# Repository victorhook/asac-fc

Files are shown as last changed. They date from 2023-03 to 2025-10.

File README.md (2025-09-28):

# ASAC FC

**A** **S**imple **A**nd **C**ool **F**light **C**ontroller (**ASAC FC**) is a completely open-source flight controller that can run on multiple microcontrollers such as:
- rp2040
- rp2350

## Project goals
- [ ] Build a drone with rp2040 devboard + external IMU
- [ ] Build a drone with rp2350 devboard + external IMU
- [ ] Add Stabilize flight mode
- [ ] Add Althold flight mode (requires barometer)
- [ ] Add support for SD card logging
- [ ] UI To configure board
- [X] Separate HAL to build for different platforms (rp2040, sitl etc)

What should be configurable, and what should be built-in to firmware?
### Built-in
Must still be able to boot OK without any of these

### Configurable
- Barometer
- IMU
- RC receiver
- Motor order
- FC orientation

---

TODO: THIS GIF [ASAC Takeoff](docs/asac_takeoff.gif)

## Why rp2040?
It's an incredibly cheap microcontroller that is quite powerful (up to 133 MHz), contains two cores, programmable I/O pins (PIO), seems to ignore the global silicon shortage and has an extensive C/C++ SDK.

## Iteration 2

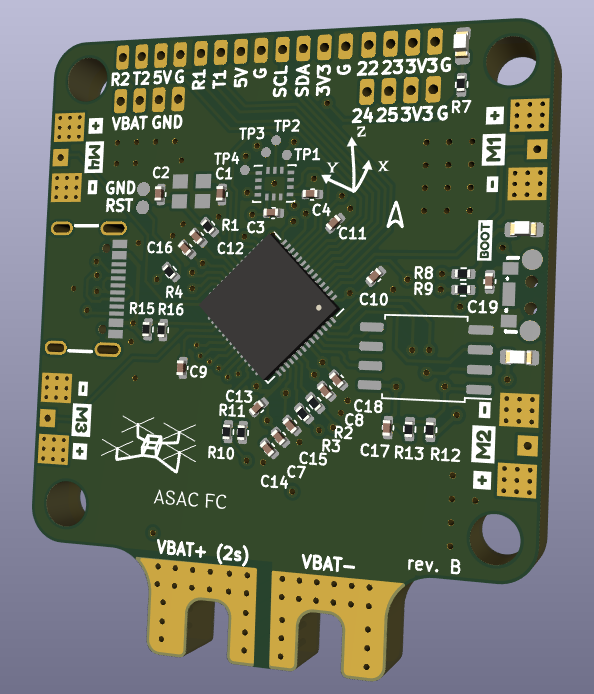
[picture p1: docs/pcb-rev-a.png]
ASAC rev B PCB Kicad

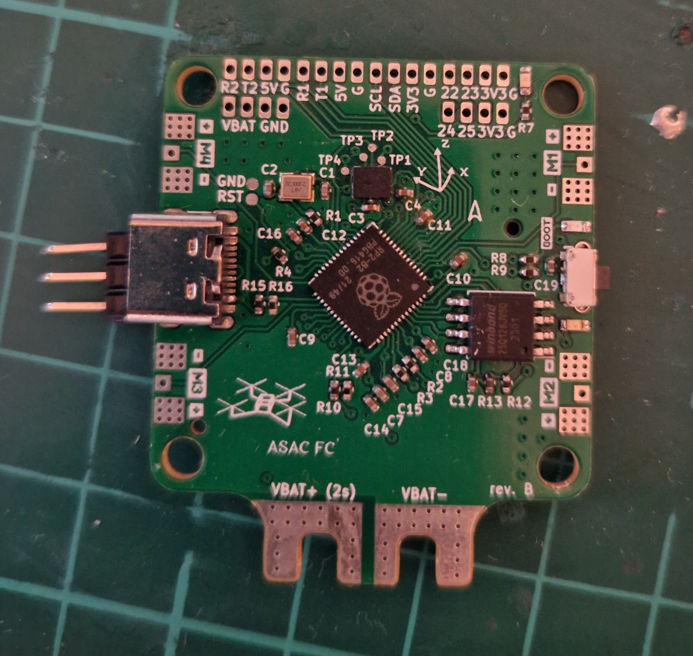
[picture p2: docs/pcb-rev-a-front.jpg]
ASAC rev B PCB front

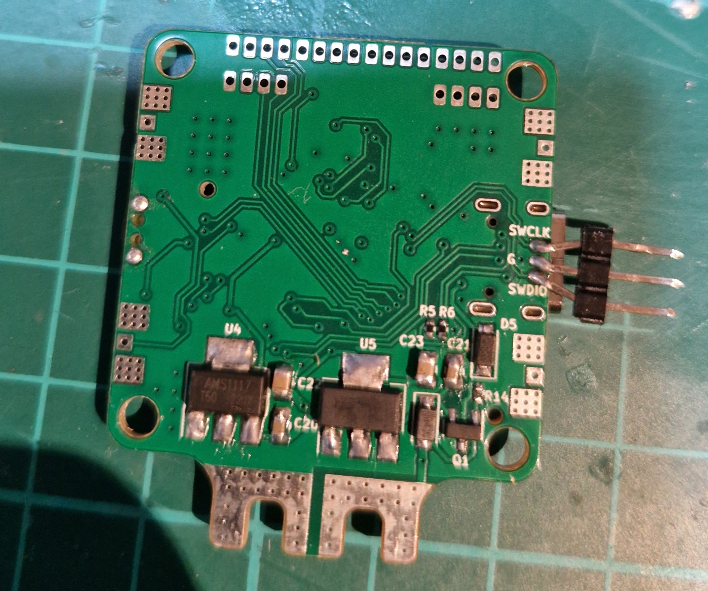
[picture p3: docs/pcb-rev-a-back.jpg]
ASAC rev B PCB back


For the second iteration of the flight controller I designed a PCB in FreeCad, ordered the pcb and components with SMD assembly for the top layer, and soldered the bottom layer myself. All cad files of this can be found in [kicad/asac-fc-rev-b](kicad/asac-fc-rev-b). Schematic can also be found at [documents/asac-fc-rev-b.pdf](documents/asac-fc-rev-b.pdf).
Some nice features of the flight controller PCB are:

- **rp2040** - Flight controller (where asac runs)
- **BMI270** - IMU, using SPI, which allows faster readings than the MPU-6050 which was used for iteration 1.
- **USB-C** - More modern, right? :)
- **Individual ESC solder pads** - Connection for individual ESCs. While most flight stacks today use an 4-in-1 ESC, I decided to keep it simple and use individual ESCs for now.
- **Battery solder pads**

## Iteration 1

The first iteration of *asac fc* was done with development boards, before designing a custom PCB. This is to make a proof of concept, and serves as a sanity check to show that it's possible :). The main components are:
- **Raspberry pi pico** - Flight controller (where asac runs)
- **MPU6050** - IMU
- **FS-a8s** - Radio receiver (Flysky, outputs IBUS)
- **xsd7a ESC** - ESCs (Single motor ESCs, so 4 in total)
- **Frame** - Custom designed, 3D-printed in PLA.

I created a simple power distribution board (brown part, at the bottom of the drone in the picture below), where the battery is connected to. Each ESC as well as the pico and the receiver gets its power from this board. The ESCs are then connected to GPIOs on the pico.

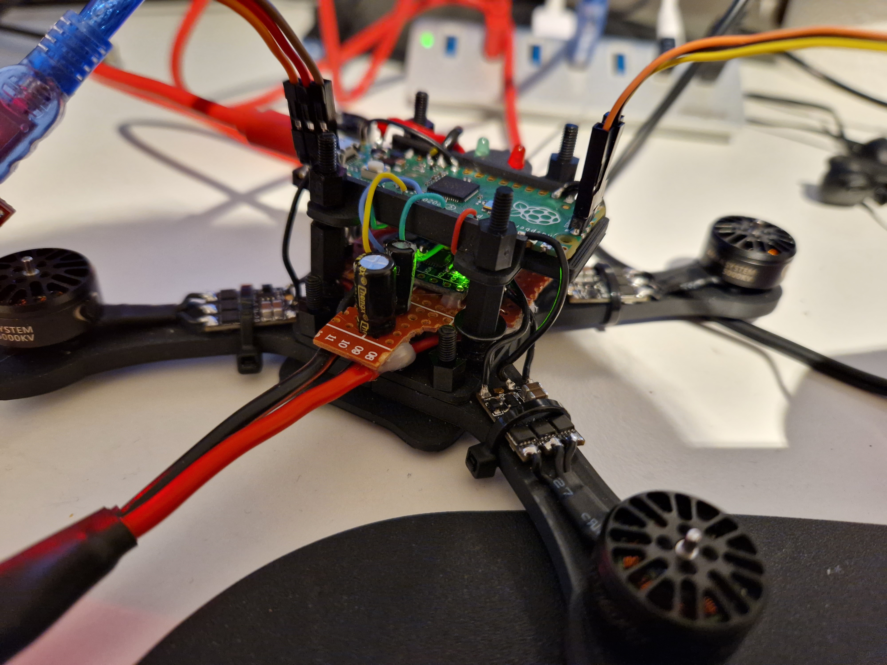
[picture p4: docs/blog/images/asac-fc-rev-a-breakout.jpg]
ASAC FC development


After some manual (headless) flights, I decided to add an analog camera together with a VTX I had laying around. This way, we can fly some FPV with the pico!

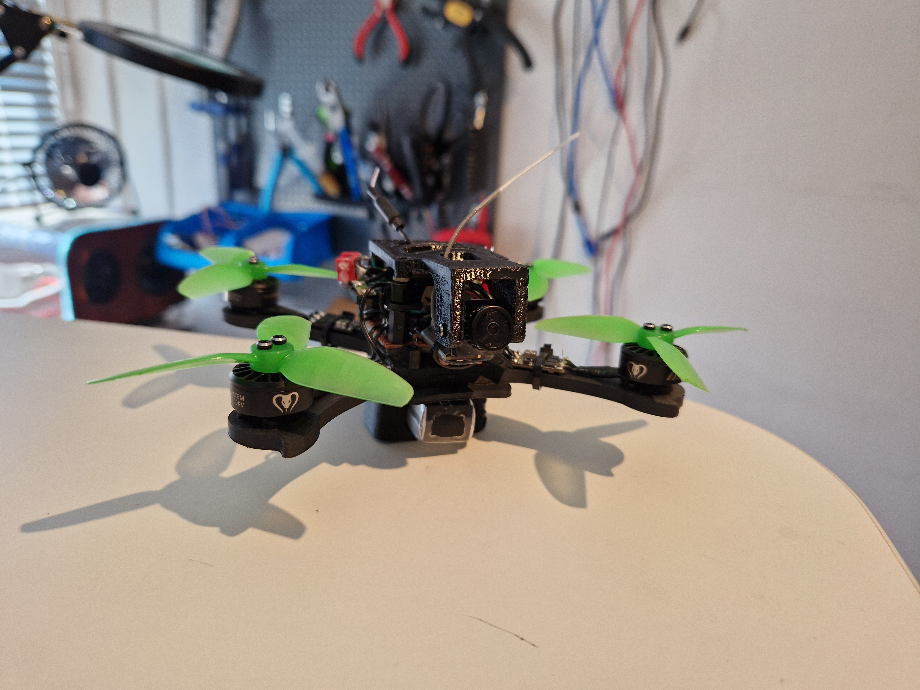
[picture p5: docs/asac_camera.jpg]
ASAC FC


## Features

### Sensors
- [X] IMU
- [ ] GPS
- [ ] Barometer (altitude estimation)
- [ ] Lidar or other distance sensor

### Receiver protocols
- [X] IBUS
- [ ] SBUS
- [ ] Frsky
- [ ] CSRF

### Telemetry
- [ ] Any

### Flight modes
- [X] Acro (attitude rate, aka free-style)
- [ ] Any other stabilizing mode

### ESC Protocols

- [X] PWM (50 hz)
- [X] Oneshot125, utilizing rp2040s PIO block
- [X] Oneshot42, utilizing rp2040s PIO block
- [ ] Multishot
- [ ] Dshot150
- [ ] Dshot300
- [ ] Dshot600
- [ ] Dshot1200
- [ ] ProShot

## From receiver input to motor outputs

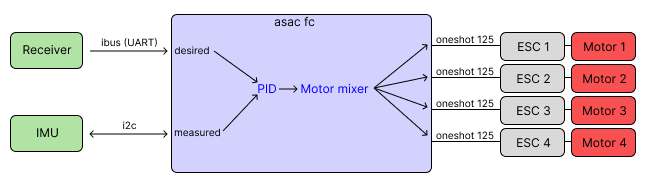
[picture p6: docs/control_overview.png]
Control overview


In order to set the correct speeds for each motor, several steps must be taken. The steps described below is how it's done for *asac fc*. Note that this is for acro mode only (freestyle, using only gyro rates from IMU).

1. Read gyro rates from IMU
2. Remove bias from gyro reading
3. Filter gyro reading
4. Read receiver input
5. Convert receiver stick inputs to desired gyro rates. This is a mapping from eg. 1000-2000 -> -500 to 500 deg/s.
6. Give the *desired* rates together with the *measured* rates to PID controller that uses PID parameters to calculate adjustment values.
7. Give output from PID controller to motor mixer to get commands for each motor.
8. Send the motor outputs to the ESC(s).

## RTOS
*asac fc* uses a very simple RTOS called [vsrtos](https://github.com/victorhook/vsrtos), that uses a priority based non-preemptive scheduling technique to run tasks. While this rtos is quite immature, it works just fine for this application, since *asac fc* doesn't have that many tasks yet.

## Motor mixing

The motor mixer is responsible for deciding which motor should spin and how much. *asac fc* uses the default motor numbers like in the image below, which is the same as the default for betaflight.

Motors

The default motor mix is:

| Motor | Throttle | Roll | Pitch | Yaw |
| --- | --- | --- | --- | --- |
| 1 | 1 | -1 | 1  | -1 |
| 2 | 1 | -1 | -1 | 1  |
| 3 | 1 | 1  | 1  | 1 |
| 4 | 1 | 1  | -1 | -1  |

## Flashing

You can flash the pico through in three different ways:
1. Through USB, when it's connected as a USB device (press down button while powering the pico)
2. Through serial USB by utilizing the picotool:
   `picotool load -f target.uf2 && picotool reboot -f`
    This works if uart 0 is mapped to USB:
    ```
    pico_enable_stdio_uart(asac-fc 0)
    pico_enable_stdio_usb(asac-fc 1)
    ```
    The command above first flashes the target `uf2` file to the pico by forcing it into BOOTSEL mode. We then reset the pico with `picotool reboot -f`. The flag `-f` is crucial here, since it allows us to load and reboot it without being in BOOTSEL mode already. I think it accomplishes this by changing the baud rate of the connection, which forces the pico to BOOTSEL mode, but I am not 100% sure.
3. SWD using debugger/another pico.

## Available build defines

There are several parameters that can be defined on build-time to configure the firmware. All of the defines can also be found in the `CMakeLists.txt` These includes:

| Define | Description |
| --- | --- |
| USE_DEFAULT_SETTINGS | If defined, asac will use default settings and write them to flash. Note that this will erase any previous settings that were stored in flash. This can be useful when using the flight controller for the first time, or updating the data structure of the flash. |
| LINUX | If defined, the firmware is built to be run on a linux machine and *not* for rp2040. This can be useful if you want to run unit tests on certain parts of code, or simulate fc. |
| RP2040 | Used by vsrtos. Do not change |

## Resources
- [Embedded Programming for Quadcopters](https://www.youtube.com/watch?v=CHSYgLfhwUo&ab_channel=Code%26Supply)
- [Motor mixing](https://oscarliang.com/custom-motor-output-mix-quadcopter/)

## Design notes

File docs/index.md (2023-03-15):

# ASAC FC

**A** **S**imple **A**nd **C**ool **F**light **C**ontroller (ASAC FC) is an flight controller based on the rp2040 microcontroller, that is completely open-source.

## From receiver input to motor outputs

In order to set the correct speeds for each motor several steps must be taken. The steps described below is how it's done for ASAC FC. Note that this is for acro mode only.

1. Read gyro rates from IMU
2. Read receiver input
3. Convert receiver stick inputs to desired gyro rates. This is a mapping from eg. 1000-2000 -> -500 to 500 deg/s.
4. Use the *desired* rates together with the *measured* rates in a pid update to update pid parameters.
5. Use the pid parameters to update the motor outputs.
6. Send the motor outputs to the ESC(s).

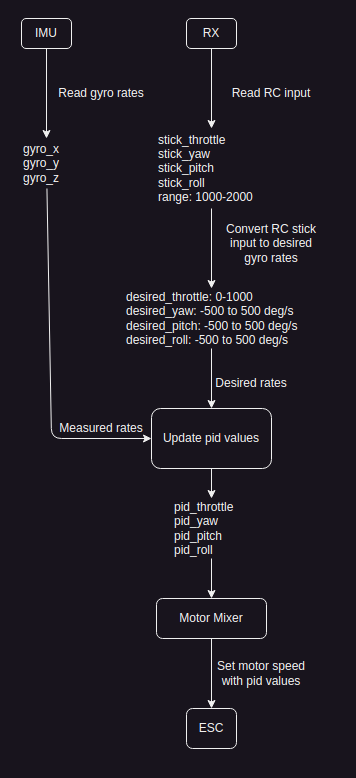
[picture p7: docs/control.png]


## Motor mixing

Motors

| Motor | Throttle | Roll | Pitch | Yaw |
| --- | --- | --- | --- | --- |
| 1 | 1 | -1 | 1  | -1 |
| 2 | 1 | -1 | -1 | 1  |
| 3 | 1 | 1  | 1  | 1 |
| 4 | 1 | 1  | -1 | -1  |

## Resources
- [Embedded Programming for Quadcopters](https://www.youtube.com/watch?v=CHSYgLfhwUo&ab_channel=Code%26Supply)
- [Motor mixing](https://oscarliang.com/custom-motor-output-mix-quadcopter/)

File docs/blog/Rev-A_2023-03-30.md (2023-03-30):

# ASAC FC revision A
For the first revision of the flight controller I designed the PCB in kicad and ordered from JLCPCB. The plan was to solder all components by hand. Unfortunately, I was out of lead-free solder and since I'm not use to working with solder *with* lead, soldering the SMD components such as the IMU (MPU-6050) turned out to be harder than I first anticipated. After several days of struggling, I gave up and switched to using breakout boards and devboard instead.

Raspberry Pi Pico to the rescue, which comes in a rather small package. I also had a breakout board for the IMU. I had to create a power distribution board as well, where the battery will be connected, as well as the ESCs. Even though this does not look as good as a custom PCB, it seems to work just fine.

ASAC-FC rev A. Breakout and devboard

As you can see on the image above, the pico is mounted on top of the power distribution board, which also hosts the IMU and radio receiver. To program the pico I used a [pico debug probe](https://www.raspberrypi.com/products/debug-probe/) and then connected GPIO0 and GPIO1, which are default UART pins, to an FTDI converter connected to my PC.

This way, it was very convenient to program the flash, while constantly being connected to a serial port to its UART, and also having the capability of debugging in VS Code.

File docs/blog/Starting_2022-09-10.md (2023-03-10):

## Introduction
I've built and flown FPV drones for a few years now as a happy and I truly enjoy both building them and flying then. Usually, I end up spending more time building the drones and fixing/repairing them than actually flying then, but for me that is very satisfying. So, during the last two years or so, the prices of electronics for FPV drones has almost doubled. I remember that I bought the first stack of FC + ESC for about 40$, and the very same stack goes for around 70-80$ today. This increase in price together with my own curiosity and maker-mind has made me wanting to build my own FPV electronics for some time, and now it's finally time to take fhe first step!

This is the journey for me building my very first flight controller hardware for an FPV drone. I will design the schematics and PCB in KiCad and order them, together with components, which I will then solder (by hand probably). I'm planning to write my firmware for the FC as well, mainly because I think it's interesting and a fun challenge. My idea is that I will start by making the flight controller, and making the first revision of the drone with my custom flight controller, and all the other parts will be off-the-shelf. Then, perhaps I can create my custom ESC, custom RX, VTX etc, so in the end I will have only custom electronics on my FPV drones! This will probably take a long time however, so for now, let's focus on the flight controller.

## Flight Controller, rev. A
For the first revision, I will have the following main components of the flight controller:
| Component | Description | Motivation |
| --- | --- | --- |
| rp2040 | Main microcontroller | *Very* cheap mcu which is quite new on the market. It has two cores, and I've wanted to use the rp2040 for custom projects for some time now. Since it's supported by the raspberry pi community it has extensive documentation as well as a C SDK. How well this will perform to the famous STM32F4 I do not know yet, so we will have to find out! One thing that does worry me slightly is the lack of UART buses. The rp2040 only has 2 UART buses, *but* it does have programmable IO, which I believe can handle UART communication as well, so it might be possible to extend these 2 buses to more.
| MPU-6050 | Inertial Measurement Unit (IMU) | The famous MPU-6050 must be one of the most popular IMUs for makers in general and on flight controllers. The reason I chose this was simply because I had bought a pack of 10 of these some time ago so I had them laying around. The support for MPU-6050 (in forms of drivers, documentation etc) as well is extensive so there should be no problem to set it up. An important note is that the MPU-6050 is very old and no longer produced, so if this flight controller ever were to become a product, the MPU-6050 must be changed.

Here's some bullet points about some design decisions for revision A:
- There's no OSD chip like MAX7456, or SD card holder simply to keep the scope and complexity down.
- There's solder pads for individual ESCs. Mainly because I had some individual ESCs at home I wanted to use.
- Keep it simple!

Since there's no OSD chip on rev A, I will mainly use this revision to try to get the most basic drone flying working.

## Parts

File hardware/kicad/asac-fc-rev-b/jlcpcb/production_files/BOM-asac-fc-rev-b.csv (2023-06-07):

Comment | Designator | Footprint | LCSC
5.11k | R6 | R_0402_1005Metric
5.11k | R5 | R_0402_1005Metric
D_Schottky | D5 | D_SOD-123
USB_C_Receptacle_USB2.0 | J10 | USB-SMD_GT-USB-7010AN
BMI270 | U1 | BMI270
W25Q128JVSIQ | U3 | SOIC-8_5.23x5.23mm_P1.27mm
30pF | C2 | C_0402_1005Metric
100nF | C13 | C_0402_1005Metric
Conn_01x03 | J4 | Conn_01x03_2big_1small
100nF | C18 | C_0402_1005Metric
Conn_01x03 | J9 | Conn_01x03_2big_1small
330R | R8 | R_0402_1005Metric
330R | R9 | R_0402_1005Metric
100nF | C14 | C_0402_1005Metric
100nF | C12 | C_0402_1005Metric
100nF | C16 | C_0402_1005Metric
Conn_01x02 | J7 | Conn_01x02_small
SW_SPST | SW1 | SW-SMD_TS-1086EV-16
1k | R1 | R_0402_1005Metric
LED | D3 | LED_0603_no_outline
1uF | C7 | C_0402_1005Metric
10k | R4 | R_0402_1005Metric
100nF | C9 | C_0402_1005Metric
Conn_01x03 | J1 | Conn_01x03_2big_1small
27.4R | R3 | R_0402_1005Metric
Conn_01x04 | J15 | Conn_01x04_fpv
1k | R12 | R_0402_1005Metric
10k | R13 | R_0402_1005Metric
CM4012M00020T8188087 | Y1 | Crystal_SMD_2520-4Pin_2.5x2.0mm
RP2040 | U2 | QFN-56-1EP_7x7mm_P0.4mm_EP3.2x3.2mm
1uF | C15 | C_0402_1005Metric
Conn_01x04 | J2 | Conn_01x04_fpv
Conn_01x03 | J14 | PinHeader_1x03_P1.27mm_Vertical_no_silk_smd
10k | R10 | R_0402_1005Metric
Conn_01x04 | J8 | Conn_01x04_fpv
27.4R | R2 | R_0402_1005Metric
100nF | C4 | C_0402_1005Metric
5.6k | R11 | R_0402_1005Metric
100nF | C11 | C_0402_1005Metric
100nF | C8 | C_0402_1005Metric
Conn_01x03 | J6 | Conn_01x03_2big_1small
30pF | C1 | C_0402_1005Metric
LED | D1 | LED_0603_no_outline
Conn_01x04 | J5 | Conn_01x04_fpv
100nF | C17 | C_0402_1005Metric
LED | D2 | LED_0603_no_outline
330R | R7 | R_0402_1005Metric
100nF | C10 | C_0402_1005Metric
Conn_01x04 | J12 | Conn_01x04_fpv
100nF | C3 | C_0402_1005Metric
100nF | C19 | C_0402_1005Metric
AMS1117-5.0 | U4 | SOT-223-3_TabPin2
10uF | C22 | C_0805_2012Metric
D_Schottky | D4 | D_SOD-123
10uF | C20 | C_0805_2012Metric
10uF | C21 | C_0805_2012Metric
AMS1117-3.3 | U5 | SOT-223-3_TabPin2
10uF | C23 | C_0805_2012Metric
10k | R14 | R_0402_1005Metric
Q_PMOS_GSD | Q1 | SOT-23
Conn_01x04 | J3 | Conn_01x04_fpv
TestPoint | TP4 | TP_0.7mm
TestPoint | TP3 | TP_0.7mm
TestPoint | TP2 | TP_0.7mm
TestPoint | TP1 | TP_0.7mm
20k | R16 | R_0402_1005Metric
10k | R15 | R_0402_1005Metric

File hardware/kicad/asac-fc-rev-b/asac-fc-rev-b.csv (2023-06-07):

Source: | /home/victor/coding/projects/asac-fc/kicad/asac-fc-rev-b/asac-fc-rev-b.kicad_sch
Date: | ons 7 jun 2023 19:59:35
Tool: | Eeschema 6.0.11-2627ca5db0~126~ubuntu22.04.1
Generator: | /usr/share/kicad/plugins/bom_csv_grouped_by_value.py
Component Count: | 67
Individual Components:
Item | Qty | Reference(s) | Value | LibPart | Footprint | Datasheet | MANUFACTURER | MAXIMUM_PACKAGE_HEIGHT | PATREV | STANDARD
 |  | C1 | 30pF | Device:C | Capacitor_SMD:C_0402_1005Metric | ~
 |  | C2 | 30pF | Device:C | Capacitor_SMD:C_0402_1005Metric | ~
 |  | C3 | 100nF | Device:C | Capacitor_SMD:C_0402_1005Metric | ~
 |  | C4 | 100nF | Device:C | Capacitor_SMD:C_0402_1005Metric | ~
 |  | C7 | 1uF | Device:C | Capacitor_SMD:C_0402_1005Metric | ~
 |  | C8 | 100nF | Device:C | Capacitor_SMD:C_0402_1005Metric | ~
 |  | C9 | 100nF | Device:C | Capacitor_SMD:C_0402_1005Metric | ~
 |  | C10 | 100nF | Device:C | Capacitor_SMD:C_0402_1005Metric | ~
 |  | C11 | 100nF | Device:C | Capacitor_SMD:C_0402_1005Metric | ~
 |  | C12 | 100nF | Device:C | Capacitor_SMD:C_0402_1005Metric | ~
 |  | C13 | 100nF | Device:C | Capacitor_SMD:C_0402_1005Metric | ~
 |  | C14 | 100nF | Device:C | Capacitor_SMD:C_0402_1005Metric | ~
 |  | C15 | 1uF | Device:C | Capacitor_SMD:C_0402_1005Metric | ~
 |  | C16 | 100nF | Device:C | Capacitor_SMD:C_0402_1005Metric | ~
 |  | C17 | 100nF | Device:C | Capacitor_SMD:C_0402_1005Metric | ~
 |  | C18 | 100nF | Device:C | Capacitor_SMD:C_0402_1005Metric | ~
 |  | C19 | 100nF | Device:C | Capacitor_SMD:C_0402_1005Metric | ~
 |  | C20 | 10uF | Device:C | Capacitor_SMD:C_0805_2012Metric | ~
 |  | C21 | 10uF | Device:C | Capacitor_SMD:C_0805_2012Metric | ~
 |  | C22 | 10uF | Device:C | Capacitor_SMD:C_0805_2012Metric | ~
 |  | C23 | 10uF | Device:C | Capacitor_SMD:C_0805_2012Metric | ~
 |  | D1 | LED | Device:LED | Custom:LED_0603_no_outline | ~
 |  | D2 | LED | Device:LED | Custom:LED_0603_no_outline | ~
 |  | D3 | LED | Device:LED | Custom:LED_0603_no_outline | ~
 |  | D4 | D_Schottky | Device:D_Schottky | Diode_SMD:D_SOD-123 | ~
 |  | D5 | D_Schottky | Device:D_Schottky | Diode_SMD:D_SOD-123 | ~
 |  | J1 | Conn_01x03 | Connector_Generic:Conn_01x03 | Custom:Conn_01x03_2big_1small | ~
 |  | J2 | Conn_01x04 | Connector_Generic:Conn_01x04 | Custom:Conn_01x04_fpv | ~
 |  | J3 | Conn_01x04 | Connector_Generic:Conn_01x04 | Custom:Conn_01x04_fpv | ~
 |  | J4 | Conn_01x03 | Connector_Generic:Conn_01x03 | Custom:Conn_01x03_2big_1small | ~
 |  | J5 | Conn_01x04 | Connector_Generic:Conn_01x04 | Custom:Conn_01x04_fpv | ~
 |  | J6 | Conn_01x03 | Connector_Generic:Conn_01x03 | Custom:Conn_01x03_2big_1small | ~
 |  | J7 | Conn_01x02 | Connector_Generic:Conn_01x02 | Custom:Conn_01x02_small | ~
 |  | J8 | Conn_01x04 | Connector_Generic:Conn_01x04 | Custom:Conn_01x04_fpv | ~
 |  | J9 | Conn_01x03 | Connector_Generic:Conn_01x03 | Custom:Conn_01x03_2big_1small | ~
 |  | J10 | USB_C_Receptacle_USB2.0 | Connector:USB_C_Receptacle_USB2.0 | Custom:USB-SMD_GT-USB-7010AN | https://www.lcsc.com/product-detail/span-style-background-color-ff0-USB-span-Connectors_G-Switch-GT-USB-7010AN_C963370.html
 |  | J12 | Conn_01x04 | Connector_Generic:Conn_01x04 | Custom:Conn_01x04_fpv | ~
 |  | J14 | Conn_01x03 | Connector_Generic:Conn_01x03 | Custom:PinHeader_1x03_P1.27mm_Vertical_no_silk_smd | ~
 |  | J15 | Conn_01x04 | Connector_Generic:Conn_01x04 | Custom:Conn_01x04_fpv | ~
 |  | Q1 | Q_PMOS_GSD | Device:Q_PMOS_GSD | Package_TO_SOT_SMD:SOT-23 | ~
 |  | R1 | 1k | Device:R | Resistor_SMD:R_0402_1005Metric | ~
 |  | R2 | 27.4R | Device:R | Resistor_SMD:R_0402_1005Metric | ~
 |  | R3 | 27.4R | Device:R | Resistor_SMD:R_0402_1005Metric | ~
 |  | R4 | 10k | Device:R | Resistor_SMD:R_0402_1005Metric | ~
 |  | R5 | 5.11k | Device:R | Resistor_SMD:R_0402_1005Metric | ~
 |  | R6 | 5.11k | Device:R | Resistor_SMD:R_0402_1005Metric | ~
 |  | R7 | 330R | Device:R | Resistor_SMD:R_0402_1005Metric | ~
 |  | R8 | 330R | Device:R | Resistor_SMD:R_0402_1005Metric | ~
 |  | R9 | 330R | Device:R | Resistor_SMD:R_0402_1005Metric | ~
 |  | R10 | 10k | Device:R | Resistor_SMD:R_0402_1005Metric | ~
 |  | R11 | 5.6k | Device:R | Resistor_SMD:R_0402_1005Metric | ~
 |  | R12 | 1k | Device:R | Resistor_SMD:R_0402_1005Metric | ~
 |  | R13 | 10k | Device:R | Resistor_SMD:R_0402_1005Metric | ~
 |  | R14 | 10k | Device:R | Resistor_SMD:R_0402_1005Metric | ~
 |  | R15 | 10k | Device:R | Resistor_SMD:R_0402_1005Metric | ~
 |  | R16 | 20k | Device:R | Resistor_SMD:R_0402_1005Metric | ~
 |  | SW1 | SW_SPST | Switch:SW_SPST | Custom:SW-SMD_TS-1086EV-16 | ~
 |  | TP1 | TestPoint | Connector:TestPoint | Custom:TP_0.7mm | ~
 |  | TP2 | TestPoint | Connector:TestPoint | Custom:TP_0.7mm | ~
 |  | TP3 | TestPoint | Connector:TestPoint | Custom:TP_0.7mm | ~
 |  | TP4 | TestPoint | Connector:TestPoint | Custom:TP_0.7mm | ~
 |  | U1 | BMI270 | Custom2:BMI270 | Custom:BMI270 |  | Bosch Sensortec | 0.87mm | 1.0 | Manufacturer Recommendations
 |  | U2 | RP2040 | MCU_RaspberryPi:RP2040 | Package_DFN_QFN:QFN-56-1EP_7x7mm_P0.4mm_EP3.2x3.2mm | https://datasheets.raspberrypi.com/rp2040/rp2040-datasheet.pdf
 |  | U3 | W25Q128JVSIQ | Memory_Flash:W25Q128JVS | Package_SO:SOIC-8_5.23x5.23mm_P1.27mm | https://datasheet.lcsc.com/lcsc/1811142111_Winbond-Elec-W25Q128JVSIQ_C97521.pdf
 |  | U4 | AMS1117-5.0 | Regulator_Linear:AMS1117-5.0 | Package_TO_SOT_SMD:SOT-223-3_TabPin2 | http://www.advanced-monolithic.com/pdf/ds1117.pdf
 |  | U5 | AMS1117-3.3 | Regulator_Linear:AMS1117-3.3 | Package_TO_SOT_SMD:SOT-223-3_TabPin2 | http://www.advanced-monolithic.com/pdf/ds1117.pdf
 |  | Y1 | CM4012M00020T8188087 | Device:Crystal_GND24 | Crystal:Crystal_SMD_2520-4Pin_2.5x2.0mm | ~
Collated Components:
Item | Qty | Reference(s) | Value | LibPart | Footprint | Datasheet | MANUFACTURER | MAXIMUM_PACKAGE_HEIGHT | PATREV | STANDARD
1 | 2 | C1, C2 | 30pF | Device:C | Capacitor_SMD:C_0402_1005Metric | ~
2 | 13 | C3, C4, C8, C9, C10, C11, C12, C13, C14, C16, C17, C18, C19 | 100nF | Device:C | Capacitor_SMD:C_0402_1005Metric | ~
3 | 2 | C7, C15 | 1uF | Device:C | Capacitor_SMD:C_0402_1005Metric | ~
4 | 4 | C20, C21, C22, C23 | 10uF | Device:C | Capacitor_SMD:C_0805_2012Metric | ~
5 | 3 | D1, D2, D3 | LED | Device:LED | Custom:LED_0603_no_outline | ~
6 | 2 | D4, D5 | D_Schottky | Device:D_Schottky | Diode_SMD:D_SOD-123 | ~
7 | 4 | J1, J4, J6, J9 | Conn_01x03 | Connector_Generic:Conn_01x03 | Custom:Conn_01x03_2big_1small | ~
8 | 6 | J2, J3, J5, J8, J12, J15 | Conn_01x04 | Connector_Generic:Conn_01x04 | Custom:Conn_01x04_fpv | ~
9 | 1 | J7 | Conn_01x02 | Connector_Generic:Conn_01x02 | Custom:Conn_01x02_small | ~
10 | 1 | J10 | USB_C_Receptacle_USB2.0 | Connector:USB_C_Receptacle_USB2.0 | Custom:USB-SMD_GT-USB-7010AN | https://www.lcsc.com/product-detail/span-style-background-color-ff0-USB-span-Connectors_G-Switch-GT-USB-7010AN_C963370.html
11 | 1 | J14 | Conn_01x03 | Connector_Generic:Conn_01x03 | Custom:PinHeader_1x03_P1.27mm_Vertical_no_silk_smd | ~
12 | 1 | Q1 | Q_PMOS_GSD | Device:Q_PMOS_GSD | Package_TO_SOT_SMD:SOT-23 | ~
13 | 2 | R1, R12 | 1k | Device:R | Resistor_SMD:R_0402_1005Metric | ~
14 | 2 | R2, R3 | 27.4R | Device:R | Resistor_SMD:R_0402_1005Metric | ~
15 | 5 | R4, R10, R13, R14, R15 | 10k | Device:R | Resistor_SMD:R_0402_1005Metric | ~
16 | 2 | R5, R6 | 5.11k | Device:R | Resistor_SMD:R_0402_1005Metric | ~
17 | 3 | R7, R8, R9 | 330R | Device:R | Resistor_SMD:R_0402_1005Metric | ~
18 | 1 | R11 | 5.6k | Device:R | Resistor_SMD:R_0402_1005Metric | ~
19 | 1 | R16 | 20k | Device:R | Resistor_SMD:R_0402_1005Metric | ~
20 | 1 | SW1 | SW_SPST | Switch:SW_SPST | Custom:SW-SMD_TS-1086EV-16 | ~
21 | 4 | TP1, TP2, TP3, TP4 | TestPoint | Connector:TestPoint | Custom:TP_0.7mm | ~
22 | 1 | U1 | BMI270 | Custom2:BMI270 | Custom:BMI270 |  | Bosch Sensortec | 0.87mm | 1.0 | Manufacturer Recommendations
23 | 1 | U2 | RP2040 | MCU_RaspberryPi:RP2040 | Package_DFN_QFN:QFN-56-1EP_7x7mm_P0.4mm_EP3.2x3.2mm | https://datasheets.raspberrypi.com/rp2040/rp2040-datasheet.pdf
24 | 1 | U3 | W25Q128JVSIQ | Memory_Flash:W25Q128JVS | Package_SO:SOIC-8_5.23x5.23mm_P1.27mm | https://datasheet.lcsc.com/lcsc/1811142111_Winbond-Elec-W25Q128JVSIQ_C97521.pdf
25 | 1 | U4 | AMS1117-5.0 | Regulator_Linear:AMS1117-5.0 | Package_TO_SOT_SMD:SOT-223-3_TabPin2 | http://www.advanced-monolithic.com/pdf/ds1117.pdf
26 | 1 | U5 | AMS1117-3.3 | Regulator_Linear:AMS1117-3.3 | Package_TO_SOT_SMD:SOT-223-3_TabPin2 | http://www.advanced-monolithic.com/pdf/ds1117.pdf
27 | 1 | Y1 | CM4012M00020T8188087 | Device:Crystal_GND24 | Crystal:Crystal_SMD_2520-4Pin_2.5x2.0mm | ~

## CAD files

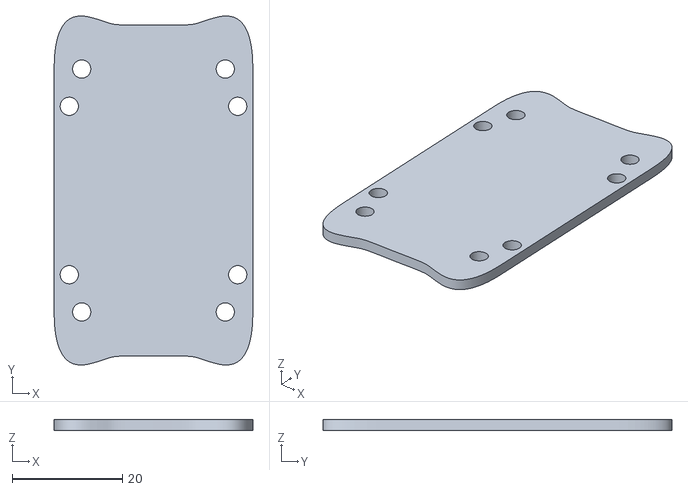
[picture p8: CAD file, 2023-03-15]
hardware/3D-print/Body-Lower.stl
36.0 x 63.2 x 2.00

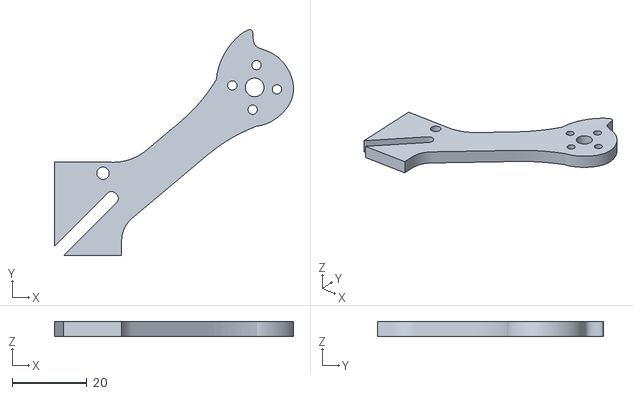
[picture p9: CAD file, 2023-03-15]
hardware/3D-print/RigthArm-rev-a.stl
64.0 x 60.5 x 4.00

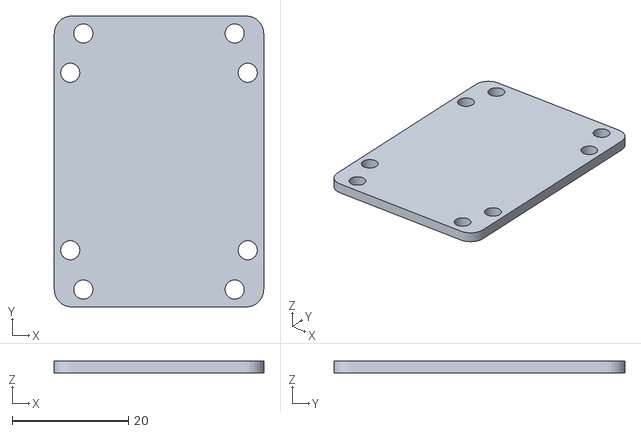
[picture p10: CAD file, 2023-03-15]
hardware/3D-print/Body-Top.stl
36.0 x 50.0 x 2.00

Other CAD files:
hardware/3D-print/LeftArm-rev-a.stl

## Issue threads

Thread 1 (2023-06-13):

Excellent FC

01Space, 2023-06-13:
I have been searching for FC using RP2040 and I really like your design. Do you use discord?
I can help you design hardware and I would like to work with you to improve RP2040 FC
https://github.com/RaisingAwesome/ArduinoNanoRP2040ConnectFlightController
This link was ported from dRehmFlight to RP2040 by other developers

01Space, 2023-06-14:
Thank you for your reply! I plan to design an RP2040 FC similar to the FPV commercial FC, which will integrate ICM42688+SPL06, as well as a 5VBEC. I am familiar with the design of RP2040 and FC,In the future, when the firmware is mature, AT7456E chip (OSD) or ELRS receiver can also be added.

victorhook, 2023-06-14:
No worries, it's fun that someone shows some interest!
I have to say I'm a bit surprised that there's so few (if any) existing flight controllers with rp2040, but it's quite new so maybe that's one of the reasons.

Sounds like a cool project you have in mind too, my first iteration I used MPU-6050, and for the second I'm going to use BMI270 for the IMU. What's your motivation behind ICM42688? :)

So far I'm not planning to integrate a baro, since I'll focus on freestyle flying, but it would be cool try to add in the future. I was looking at bmp390, but SPL06-07 seems to have very high resolution according to the datasheet (5 cm??). Do you have any experience with it?

Regarding OSD, my plan is to try to do the magic with a microcontroller instead of the using a specific IC like AT7456E, since its quite depreciated and getting hard to find. I'm taking inspiration from [this thread](https://www.rcgroups.com/forums/showthread.php?1473207-Diy-osd-%28Arduino-and-opensource%29). I'm not sure how hard it will be though, but I think it's definitely doable :)

01Space, 2023-06-15:
The pins of BMI 270 and ICM42688 are PIN to PIN, which means they can directly replace each other in hardware. Based on their performance in BF and INAV, FC manufacturers now prefer ICM42688, which performs more consistently in FC.

You can also use two ICM42688Ps with different installation angles, which can compare the data of the two sensors to reduce external interference

Of course, you can consider ICM-45686  https://invensense.tdk.com/products/motion-tracking/6-axis/icm-456xy/

For barometer SPL06_ 001 OR SPL06_ 007 can be considered, as they are widely used in BF FC and INAV FC with high cost-effectiveness. However, for some demanding FCs, they still use the more expensive MS5611

For the OSD section, we have two options,

1. Without using the simulated OSD scheme, directly let the RP2040 chip output data to DJI O3 through the serial port
2. Refer to this design  https://github.com/spracing/spracingpixelosd

Of course, currently the most important thing is to support the CRSF receiver protocol and enable FC to have stabilization Flight modes

You can also consider referencing this project https://github.com/nickrehm/dRehmFlight

victorhook, 2023-06-17:
Interesting regarding ICM42688, seems like it costs slightly more than BMI270 (which goes for ~2$?!) but good to know. It's nice if they are pin compatible.

Regarding OSD:
1. So far I'm not using anything from DJI, nor digital video, so not sure how this would work. I probably should convert to digital eventually but so far I'm still using analog.
2. That's a cool reference, I'll definitely check this out :)

Regarding helping out with your arduino nano rp2040 flight controller I think I will pass as of today. I wish I had more time to spend on projects like this, but I think that the time I have I will spend on this project. My "long-term goal" is to build all (at least most) electronic parts for an FPV drone myself, including FC, ESC, RX, VTX etc. I've just did a first revision of a custom [ESC](https://github.com/victorhook/asac-esc) that I hope I can use with this FC :)

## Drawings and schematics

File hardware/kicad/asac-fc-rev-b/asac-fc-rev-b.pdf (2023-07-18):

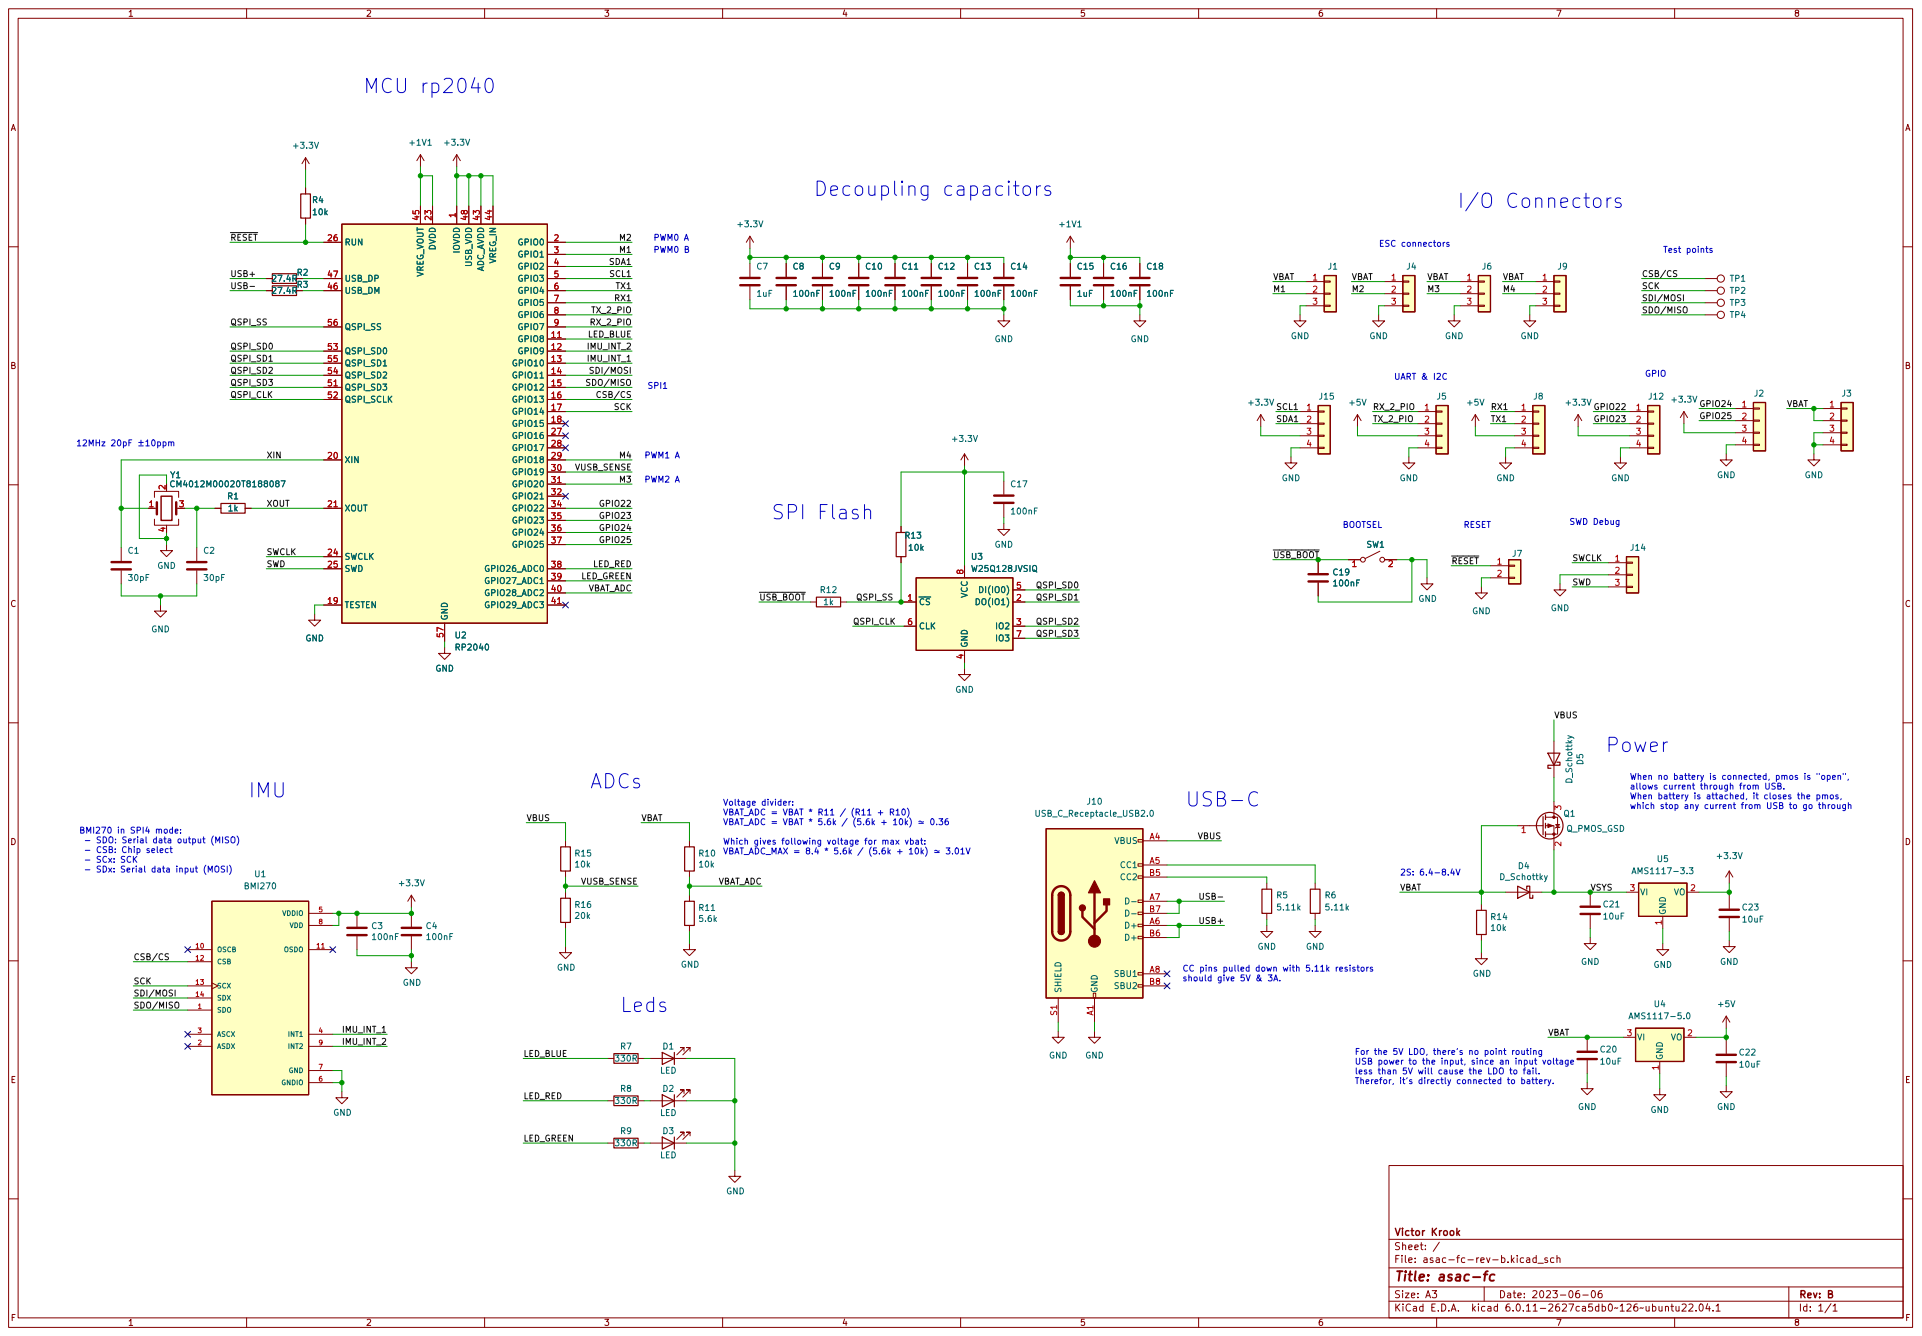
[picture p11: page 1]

Test points SWD Debug CC pins pulled down with 5.11k resistors

BMI270 in SPI4 mode: - SDO: Serial data output (MISO)

- CSB: Chip select - SCx: SCK

- SDx: Serial data input (MOSI)

For the 5V LDO, there's no point routing USB power to the input, since an input voltage

Id: 1/1 Title: asac-fc

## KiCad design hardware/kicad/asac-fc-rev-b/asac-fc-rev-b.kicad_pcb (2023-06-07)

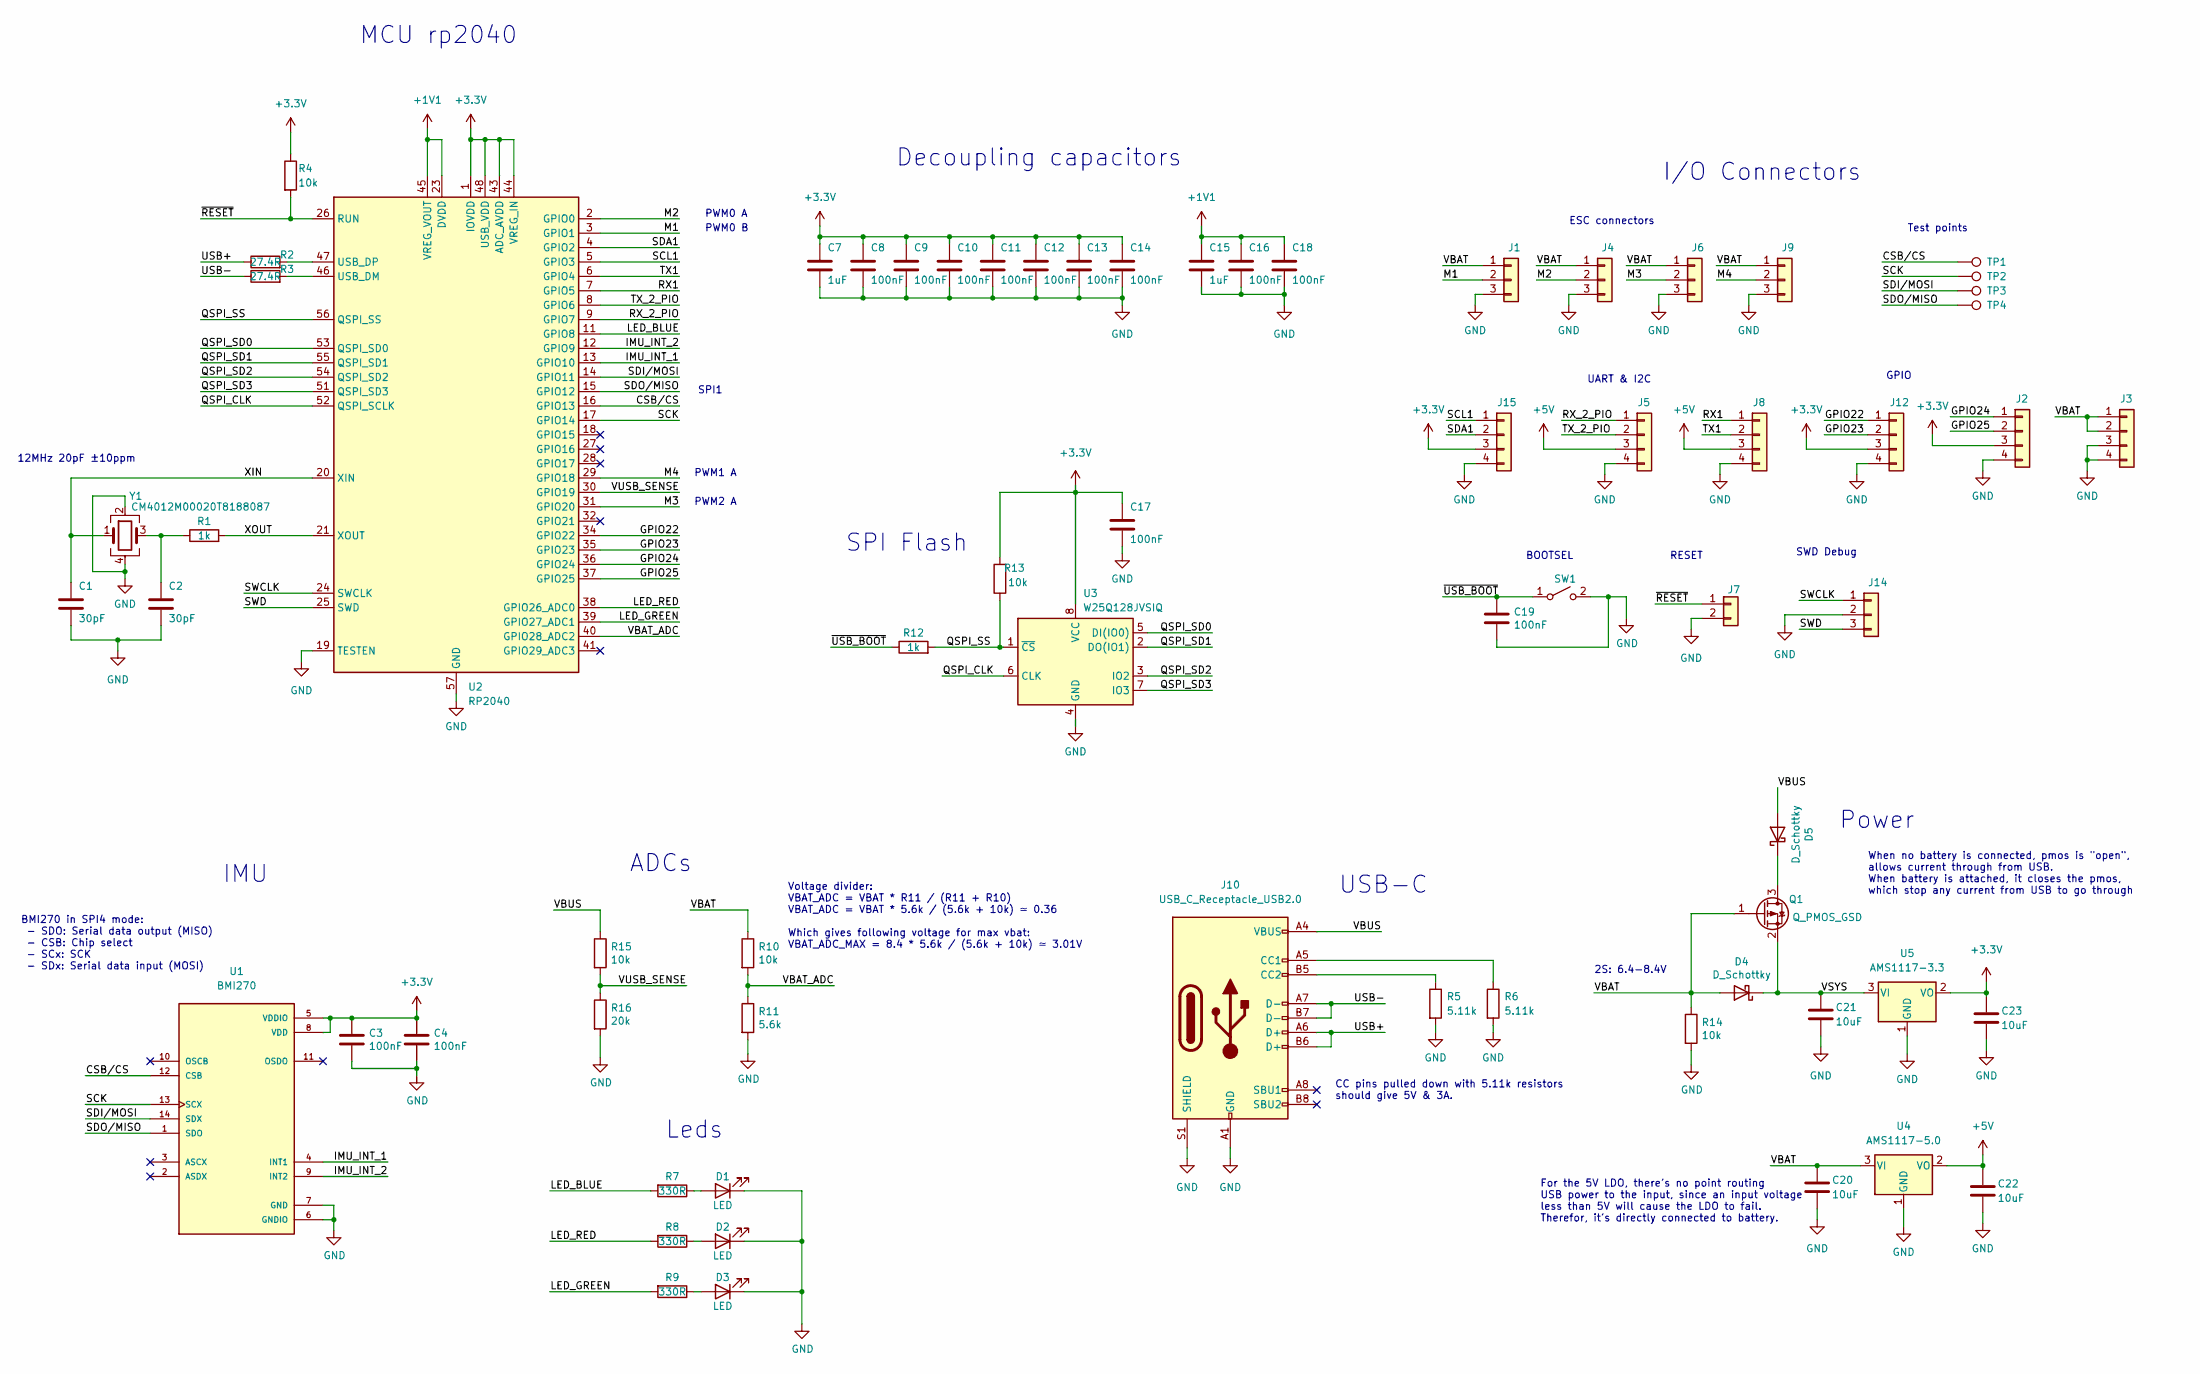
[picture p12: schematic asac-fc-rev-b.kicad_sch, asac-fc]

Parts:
C1, C2: 30pF; C_0402_1005Metric
C3, C4, C8, C9, C10, C11, C12, C13, C14, C16, C17, C18, C19: 100nF; C_0402_1005Metric
C7, C15: 1uF; C_0402_1005Metric
C20, C21, C22, C23: 10uF; C_0805_2012Metric
D1, D2, D3: LED; LED_0603_no_outline
D4, D5: D_Schottky; D_SOD-123
J1, J4, J6, J9: Conn_01x03; Conn_01x03_2big_1small
J2, J3, J5, J8, J12, J15: Conn_01x04; Conn_01x04_fpv
J7: Conn_01x02; Conn_01x02_small
J10: USB_C_Receptacle_USB2.0; USB-SMD_GT-USB-7010AN
J14: Conn_01x03; PinHeader_1x03_P1.27mm_Vertical_no_silk_smd
Q1: Q_PMOS_GSD; SOT-23
R1, R12: 1k; R_0402_1005Metric
R2, R3: 27.4R; R_0402_1005Metric
R4, R10, R13, R14, R15: 10k; R_0402_1005Metric
R5, R6: 5.11k; R_0402_1005Metric
R7, R8, R9: 330R; R_0402_1005Metric
R11: 5.6k; R_0402_1005Metric
R16: 20k; R_0402_1005Metric
SW1: SW_SPST; SW-SMD_TS-1086EV-16
TP1, TP2, TP3, TP4: TestPoint; TP_0.7mm
U1: BMI270
U2: RP2040; QFN-56-1EP_7x7mm_P0.4mm_EP3.2x3.2mm
U3: W25Q128JVSIQ; SOIC-8_5.23x5.23mm_P1.27mm
U4: AMS1117-5.0; SOT-223-3_TabPin2
U5: AMS1117-3.3; SOT-223-3_TabPin2
Y1: CM4012M00020T8188087; Crystal_SMD_2520-4Pin_2.5x2.0mm

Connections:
+1V1: C15.1, C16.1, C18.1, U2.23 (DVDD), U2.45 (VREG_VOUT), U2.50 (DVDD)
+3.3V: C3.1, C4.1, C7.1, C8.1, C9.1, C10.1, C11.1, C12.1, C13.1, C14.1, C17.1, C23.1, J2.3, J12.3, J15.3, R4.1, R13.2, U1.5 (VDDIO), U1.8 (VDD), U2.1 (IOVDD), U2.10 (IOVDD), U2.22 (IOVDD), U2.33 (IOVDD), U2.42 (IOVDD), U2.43 (ADC_AVDD), U2.44 (VREG_IN), U2.48 (USB_VDD), U2.49 (IOVDD), U3.8 (VCC), U5.2 (VO)
+5V: C22.1, J5.3, J8.3, U4.2 (VO)
/CSB/CS: TP1.1, U1.12 (CSB), U2.16 (GPIO13)
/GPIO22: J12.1, U2.34 (GPIO22)
/GPIO23: J12.2, U2.35 (GPIO23)
/GPIO24: J2.1, U2.36 (GPIO24)
/GPIO25: J2.2, U2.37 (GPIO25)
/IMU_INT_1: U1.4 (INT1), U2.13 (GPIO10)
/IMU_INT_2: U1.9 (INT2), U2.12 (GPIO9)
/LED_BLUE: R7.2, U2.11 (GPIO8)
/LED_GREEN: R9.2, U2.39 (GPIO27_ADC1)
/LED_RED: R8.2, U2.38 (GPIO26_ADC0)
/M1: J1.2, U2.3 (GPIO1)
/M2: J4.2, U2.2 (GPIO0)
/M3: J6.2, U2.31 (GPIO20)
/M4: J9.2, U2.29 (GPIO18)
/QSPI_CLK: U2.52 (QSPI_SCLK), U3.6 (CLK)
/QSPI_SD0: U2.53 (QSPI_SD0), U3.5 (DI(IO0))
/QSPI_SD1: U2.55 (QSPI_SD1), U3.2 (DO(IO1))
/QSPI_SD2: U2.54 (QSPI_SD2), U3.3 (IO2)
/QSPI_SD3: U2.51 (QSPI_SD3), U3.7 (IO3)
/QSPI_SS: R12.2, R13.1, U2.56 (QSPI_SS), U3.1 (~CS)
/RX1: J8.1, U2.7 (GPIO5)
/RX_2_PIO: J5.1, U2.9 (GPIO7)
/SCK: TP2.1, U1.13 (SCX), U2.17 (GPIO14)
/SCL1: J15.1, U2.5 (GPIO3)
/SDA1: J15.2, U2.4 (GPIO2)
/SDI/MOSI: TP3.1, U1.14 (SDX), U2.14 (GPIO11)
/SDO/MISO: TP4.1, U1.1 (SDO), U2.15 (GPIO12)
/SWCLK: J14.1, U2.24 (SWCLK)
/SWD: J14.3, U2.25 (SWD)
/TX1: J8.2, U2.6 (GPIO4)
/TX_2_PIO: J5.2, U2.8 (GPIO6)
/USB+: J10.A6 (D+), J10.B6 (D+), R2.1
/USB-: J10.A7 (D-), J10.B7 (D-), R3.1
/VBAT: C20.1, D4.2 (A), J1.1, J3.1, J3.2, J4.1, J6.1, J9.1, Q1.1 (G), R10.1, R14.1, U4.3 (VI)
/VBAT_ADC: R10.2, R11.1, U2.40 (GPIO28_ADC2)
/VBUS: D5.2 (A), J10.A4 (VBUS), J10.A9 (VBUS), J10.B4 (VBUS), J10.B9 (VBUS), R15.1
/VSYS: C21.1, D4.1 (K), Q1.2 (S), U5.3 (VI)
/VUSB_SENSE: R15.2, R16.1, U2.30 (GPIO19)
/XIN: C1.1, U2.20 (XIN), Y1.1
/XOUT: R1.2, U2.21 (XOUT)
/~RESET: J7.1, R4.2, U2.26 (RUN)
/~USB_BOOT: C19.1, R12.1, SW1.1 (A)
GND: C1.2, C2.2, C3.2, C4.2, C7.2, C8.2, C9.2, C10.2, C11.2, C12.2, C13.2, C14.2, C15.2, C16.2, C17.2, C18.2, C19.2, C20.2, C21.2, C22.2, C23.2, D1.1 (K), D2.1 (K), D3.1 (K), J1.3, J2.4, J3.3, J3.4, J4.3, J5.4, J6.3, J7.2, J8.4, J9.3, J10.A1 (GND), J10.A12 (GND), J10.B1 (GND), J10.B12 (GND), J10.S1 (SHIELD), J12.4, J14.2, J15.4, R5.2, R6.2, R11.2, R14.2, R16.2, SW1.2 (B), U1.6 (GNDIO), U1.7 (GND), U2.19 (TESTEN), U2.57 (GND), U3.4 (GND), U4.1 (GND), U5.1 (GND), Y1.2, Y1.4
unnamed: C2.1, R1.1, Y1.3
unnamed: D1.2 (A), R7.1
unnamed: D2.2 (A), R8.1
unnamed: D3.2 (A), R9.1
unnamed: D5.1 (K), Q1.3 (D)
unnamed: J10.A5 (CC1), R6.1
unnamed: J10.B5 (CC2), R5.1
unnamed: R2.2, U2.47 (USB_DP)
unnamed: R3.2, U2.46 (USB_DM)

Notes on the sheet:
Power
2S: 6.4-8.4V
MCU rp2040
BOOTSEL
Leds
UART & I2C
CC pins pulled down with 5.11k resistors should give 5V & 3A.
12MHz 20pF ±10ppm
PWM2 A
SPI Flash
SWD Debug
Test points
USB-C
ESC connectors
When no battery is connected, pmos is "open", allows current through from USB. When battery is attached, it closes the pmos, which stop any current from USB to go through
PWM1 A
Voltage divider: VBAT_ADC = VBAT * R11 / (R11 + R10) VBAT_ADC = VBAT * 5.6k / (5.6k + 10k) ≃ 0.36 Which gives following voltage for max vbat: VBAT_ADC_MAX = 8.4 * 5.6k / (5.6k + 10k) ≃ 3.01V
Decoupling capacitors
I/O Connectors
PWM0 A
SPI1
PWM0 B
For the 5V LDO, there's no point routing USB power to the input, since an input voltage less than 5V will cause the LDO to fail. Therefor, it's directly connected to battery.
BMI270 in SPI4 mode: - SDO: Serial data output (MISO) - CSB: Chip select - SCx: SCK - SDx: Serial data input (MOSI)
ADCs
GPIO
RESET
IMU

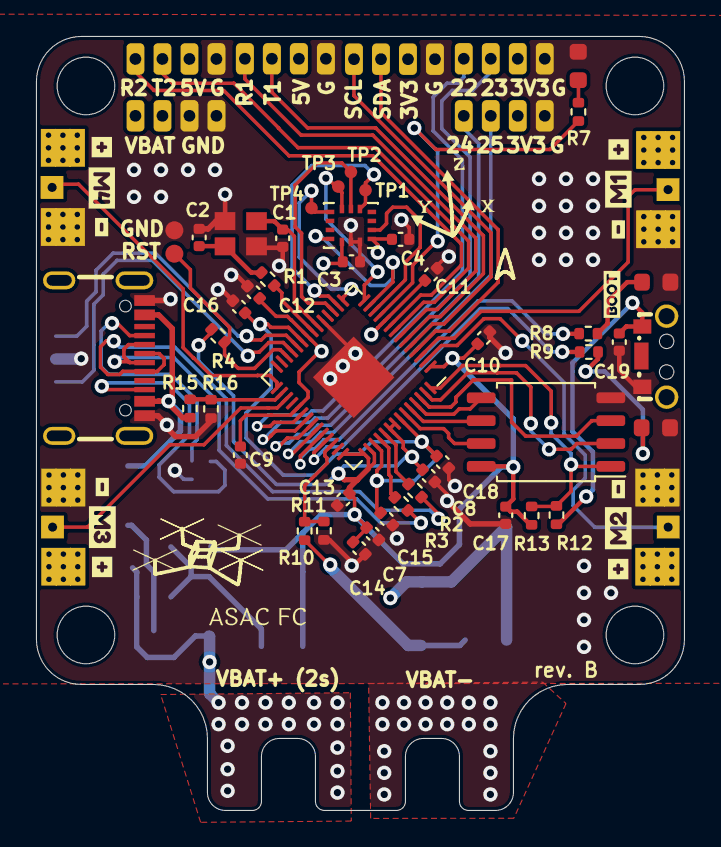
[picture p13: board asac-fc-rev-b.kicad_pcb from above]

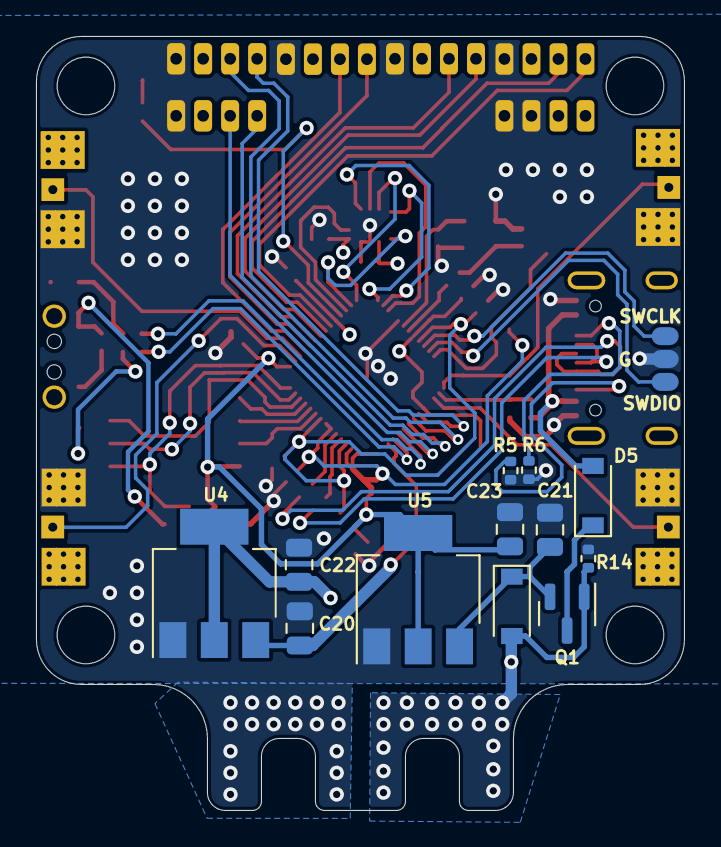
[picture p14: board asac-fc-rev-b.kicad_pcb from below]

Board: 4 copper layers, 36.0 x 43.0 mm, 80 parts (13 on the bottom side), 55 nets.

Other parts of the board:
kibuzzard-647F08DD, kibuzzard-647F08DD#2: G***; kibuzzard-647F08DD
kibuzzard-647F08EC, kibuzzard-647F08EC#2: G***; kibuzzard-647F08EC
kibuzzard-647F08F4: G***; kibuzzard-647F08F4
kibuzzard-647F09B6: G***; kibuzzard-647F09B6
kibuzzard-647F09BC: G***; kibuzzard-647F09BC
kibuzzard-647F096A, kibuzzard-647F096A#2: G***; kibuzzard-647F096A
kibuzzard-647F0963: G***; kibuzzard-647F0963
kibuzzard-647F0971, kibuzzard-647F0971#2: G***; kibuzzard-647F0971
kibuzzard-640905D0: G***; kibuzzard-640905D0

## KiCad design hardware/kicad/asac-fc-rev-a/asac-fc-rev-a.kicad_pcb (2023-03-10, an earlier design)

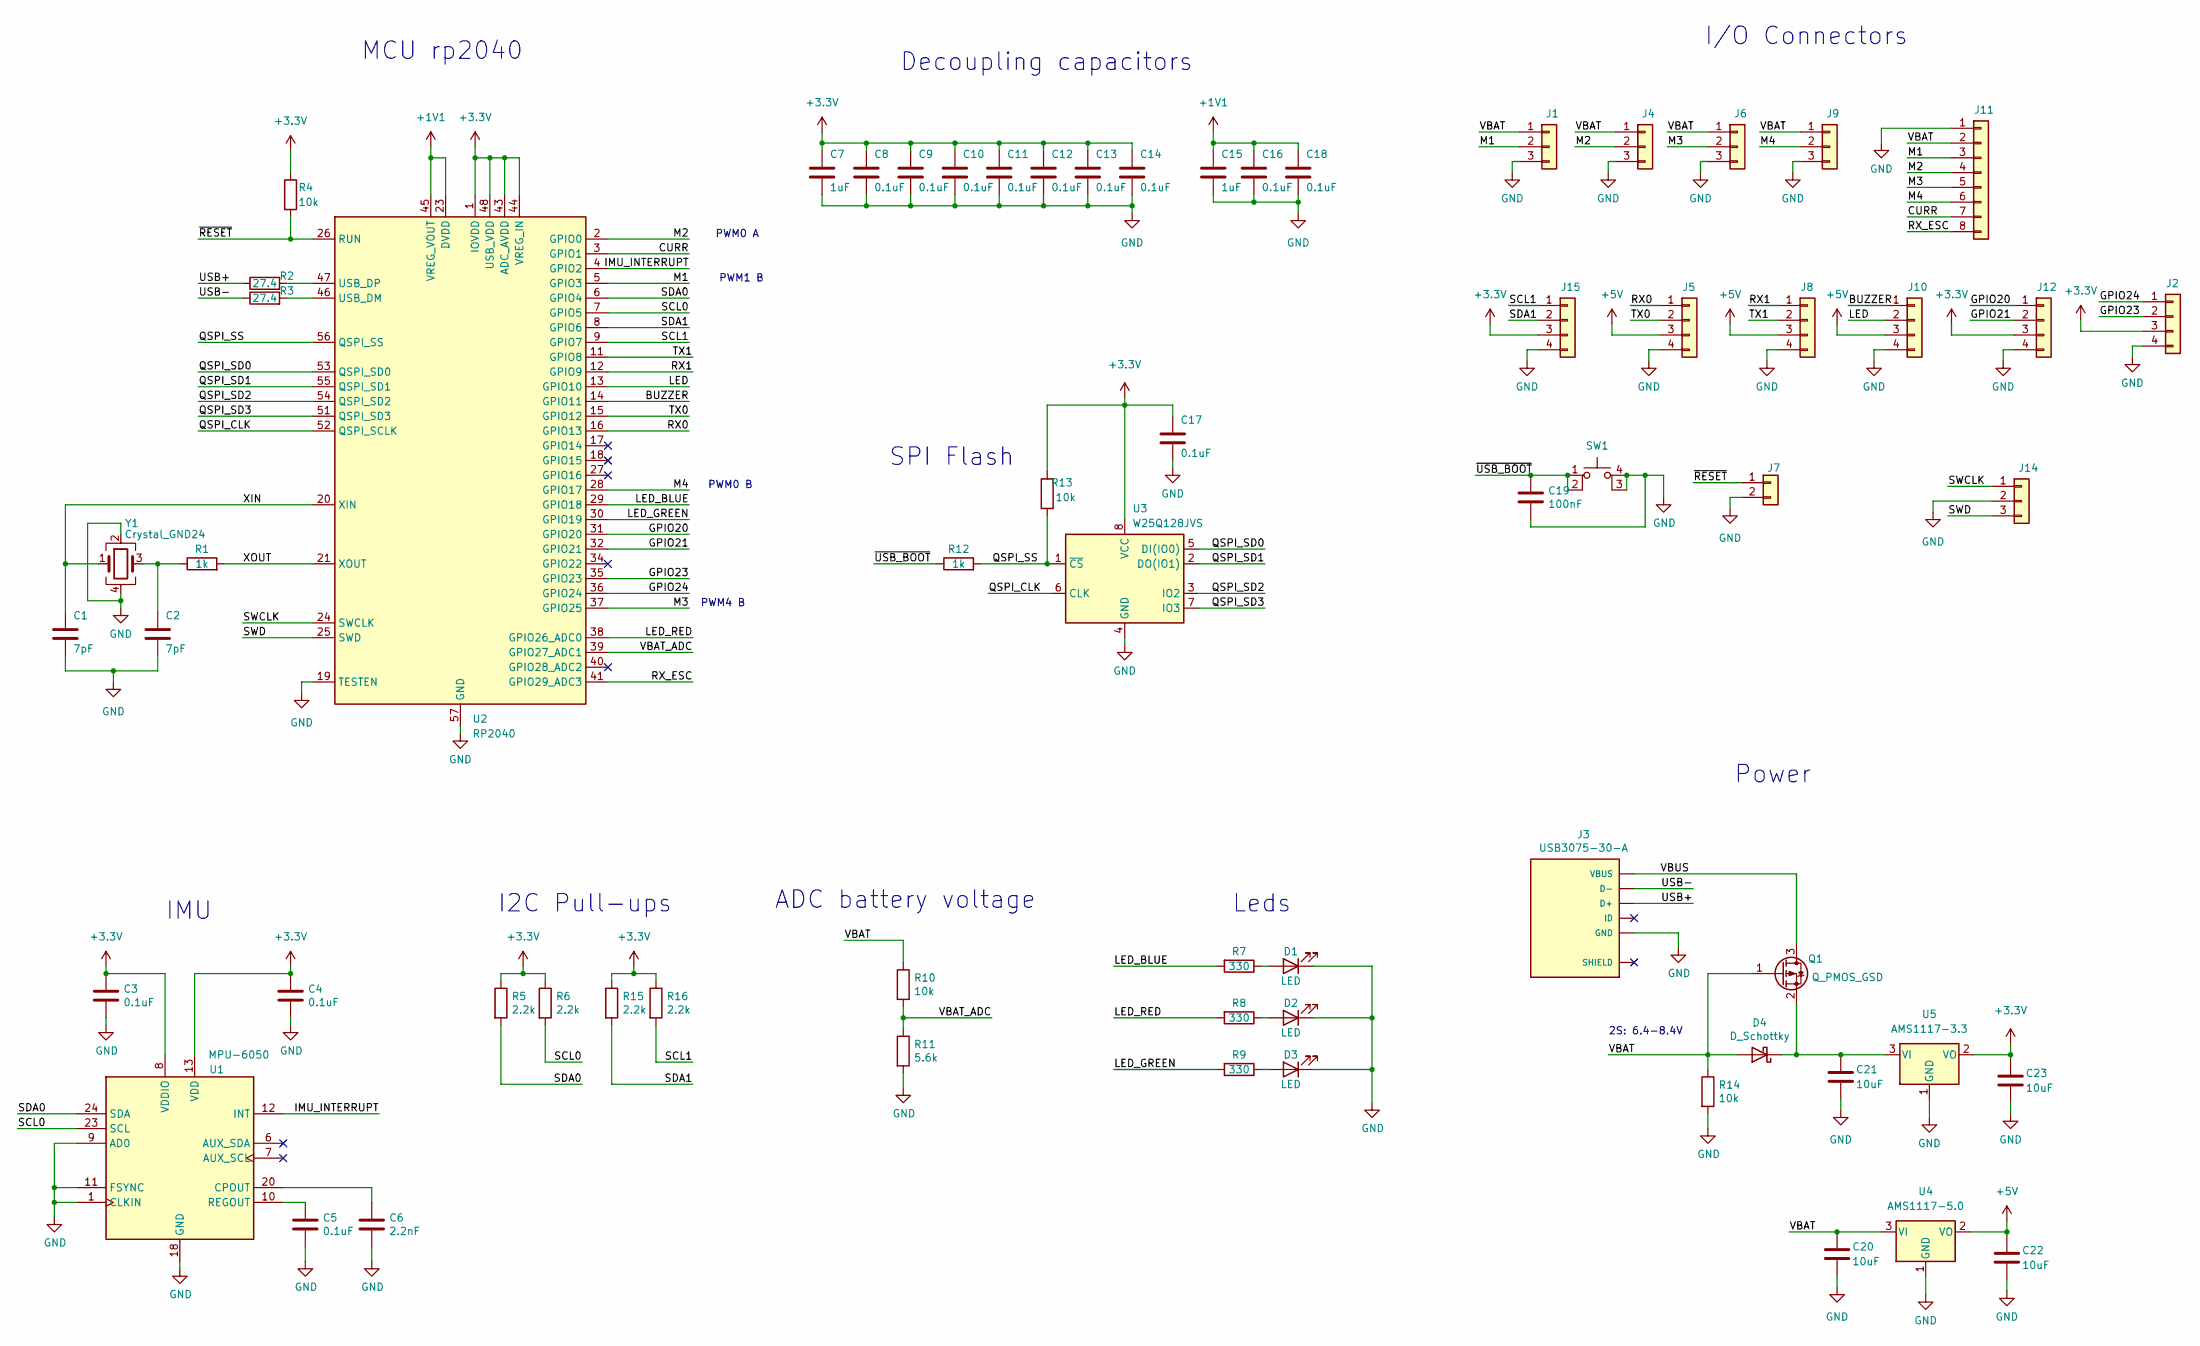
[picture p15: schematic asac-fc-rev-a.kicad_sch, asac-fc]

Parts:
C1, C2: 7pF; C_0402_1005Metric
C3, C4, C5, C8, C9, C10, C11, C12, C13, C14, C16, C17, C18: 0.1uF; C_0402_1005Metric
C6: 2.2nF; C_0402_1005Metric
C7, C15: 1uF; C_0402_1005Metric
C19: 100nF; C_0402_1005Metric
C20, C21, C22, C23: 10uF; C_0805_2012Metric
D1, D2, D3: LED; LED_0402_1005Metric_No_silk_dot
D4: D_Schottky; D_SOD-123
J1, J4, J6, J9: Conn_01x03; Conn_01x03_2big_1small
J2, J12: Conn_01x04; Conn_01x04_fpv_smd
J3: USB3075-30-A; USB3075-30-A_No_silk; PARTREV D3
J5, J8, J10, J15: Conn_01x04; Conn_01x04_fpv
J7: Conn_01x02; Conn_01x02_small
J11: Conn_01x08; JST_SH_SM08B-SRSS-TB_1x08-1MP_P1.00mm_Horizontal
J14: Conn_01x03; JST_SH_SM03B-SRSS-TB_1x03-1MP_P1.00mm_Horizontal
Q1: Q_PMOS_GSD; SOT-23
R1, R12: 1k; R_0402_1005Metric
R2, R3: 27.4; R_0402_1005Metric
R4, R10, R13, R14: 10k; R_0402_1005Metric
R5, R6, R15, R16: 2.2k; R_0402_1005Metric
R7, R8, R9: 330; R_0402_1005Metric
R11: 5.6k; R_0402_1005Metric
SW1: BOOT; PTS815
U1: MPU-6050; InvenSense_QFN-24_4x4mm_P0.5mm
U2: RP2040; QFN-56-1EP_7x7mm_P0.4mm_EP3.2x3.2mm
U3: W25Q128JVS; SOIC-8_5.23x5.23mm_P1.27mm
U4: AMS1117-5.0; SOT-223-3_TabPin2
U5: AMS1117-3.3; SOT-223-3_TabPin2
Y1: Crystal_GND24; Crystal_SMD_2016-4Pin_2.0x1.6mm

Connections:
+1V1: C15.1, C16.1, C18.1, U2.23 (DVDD), U2.45 (VREG_VOUT), U2.50 (DVDD)
+3.3V: C3.1, C4.1, C7.1, C8.1, C9.1, C10.1, C11.1, C12.1, C13.1, C14.1, C17.1, C23.1, J2.3, J12.3, J15.3, R4.1, R5.1, R6.1, R13.2, R15.1, R16.1, U1.8 (VDDIO), U1.13 (VDD), U2.1 (IOVDD), U2.10 (IOVDD), U2.22 (IOVDD), U2.33 (IOVDD), U2.42 (IOVDD), U2.43 (ADC_AVDD), U2.44 (VREG_IN), U2.48 (USB_VDD), U2.49 (IOVDD), U3.8 (VCC), U5.2 (VO)
+5V: C22.1, J5.3, J8.3, J10.3, U4.2 (VO)
/BUZZER: J10.1, U2.14 (GPIO11)
/CURR: J11.7, U2.3 (GPIO1)
/GPIO20: J12.1, U2.31 (GPIO20)
/GPIO21: J12.2, U2.32 (GPIO21)
/GPIO23: J2.2, U2.35 (GPIO23)
/GPIO24: J2.1, U2.36 (GPIO24)
/IMU_INTERRUPT: U1.12 (INT), U2.4 (GPIO2)
/LED: J10.2, U2.13 (GPIO10)
/LED_BLUE: R7.2, U2.29 (GPIO18)
/LED_GREEN: R9.2, U2.30 (GPIO19)
/LED_RED: R8.2, U2.38 (GPIO26_ADC0)
/M1: J1.2, J11.3, U2.5 (GPIO3)
/M2: J4.2, J11.4, U2.2 (GPIO0)
/M3: J6.2, J11.5, U2.37 (GPIO25)
/M4: J9.2, J11.6, U2.28 (GPIO17)
/QSPI_CLK: U2.52 (QSPI_SCLK), U3.6 (CLK)
/QSPI_SD0: U2.53 (QSPI_SD0), U3.5 (DI(IO0))
/QSPI_SD1: U2.55 (QSPI_SD1), U3.2 (DO(IO1))
/QSPI_SD2: U2.54 (QSPI_SD2), U3.3 (IO2)
/QSPI_SD3: U2.51 (QSPI_SD3), U3.7 (IO3)
/QSPI_SS: R12.2, R13.1, U2.56 (QSPI_SS), U3.1 (~CS)
/RX0: J5.1, U2.16 (GPIO13)
/RX1: J8.1, U2.12 (GPIO9)
/RX_ESC: J11.8, U2.41 (GPIO29_ADC3)
/SCL0: R6.2, U1.23 (SCL), U2.7 (GPIO5)
/SCL1: J15.1, R16.2, U2.9 (GPIO7)
/SDA0: R5.2, U1.24 (SDA), U2.6 (GPIO4)
/SDA1: J15.2, R15.2, U2.8 (GPIO6)
/SWCLK: J14.1, U2.24 (SWCLK)
/SWD: J14.3, U2.25 (SWD)
/TX0: J5.2, U2.15 (GPIO12)
/TX1: J8.2, U2.11 (GPIO8)
/USB+: J3.3 (D+), R2.1
/USB-: J3.2 (D-), R3.1
/VBAT: C20.1, D4.2 (A), J1.1, J4.1, J6.1, J9.1, J11.2, Q1.1 (G), R10.1, R14.1, U4.3 (VI)
/VBAT_ADC: R10.2, R11.1, U2.39 (GPIO27_ADC1)
/VBUS: J3.1 (VBUS), Q1.3 (D)
/XIN: C1.1, U2.20 (XIN), Y1.1
/XOUT: R1.2, U2.21 (XOUT)
/~RESET: J7.1, R4.2, U2.26 (RUN)
/~USB_BOOT: C19.1, R12.1, SW1.1, SW1.2
GND: C1.2, C2.2, C3.2, C4.2, C5.2, C6.2, C7.2, C8.2, C9.2, C10.2, C11.2, C12.2, C13.2, C14.2, C15.2, C16.2, C17.2, C18.2, C19.2, C20.2, C21.2, C22.2, C23.2, D1.1 (K), D2.1 (K), D3.1 (K), J1.3, J2.4, J3.5 (GND), J4.3, J5.4, J6.3, J7.2, J8.4, J9.3, J10.4, J11.1, J12.4, J14.2, J15.4, R11.2, R14.2, SW1.3 (K), SW1.4 (A), U1.1 (CLKIN), U1.9 (AD0), U1.11 (FSYNC), U1.18 (GND), U2.19 (TESTEN), U2.57 (GND), U3.4 (GND), U4.1 (GND), U5.1 (GND), Y1.2, Y1.4
unnamed: C2.1, R1.1, Y1.3
unnamed: C5.1, U1.10 (REGOUT)
unnamed: C6.1, U1.20 (CPOUT)
unnamed: C21.1, D4.1 (K), Q1.2 (S), U5.3 (VI)
unnamed: D1.2 (A), R7.1
unnamed: D2.2 (A), R8.1
unnamed: D3.2 (A), R9.1
unnamed: R2.2, U2.47 (USB_DP)
unnamed: R3.2, U2.46 (USB_DM)

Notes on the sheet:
Power
2S: 6.4-8.4V
MCU rp2040
IMU
Leds
PWM1 B
SPI Flash
Decoupling capacitors
I/O Connectors
PWM4 B
I2C Pull-ups
PWM0 A
ADC battery voltage
PWM0 B

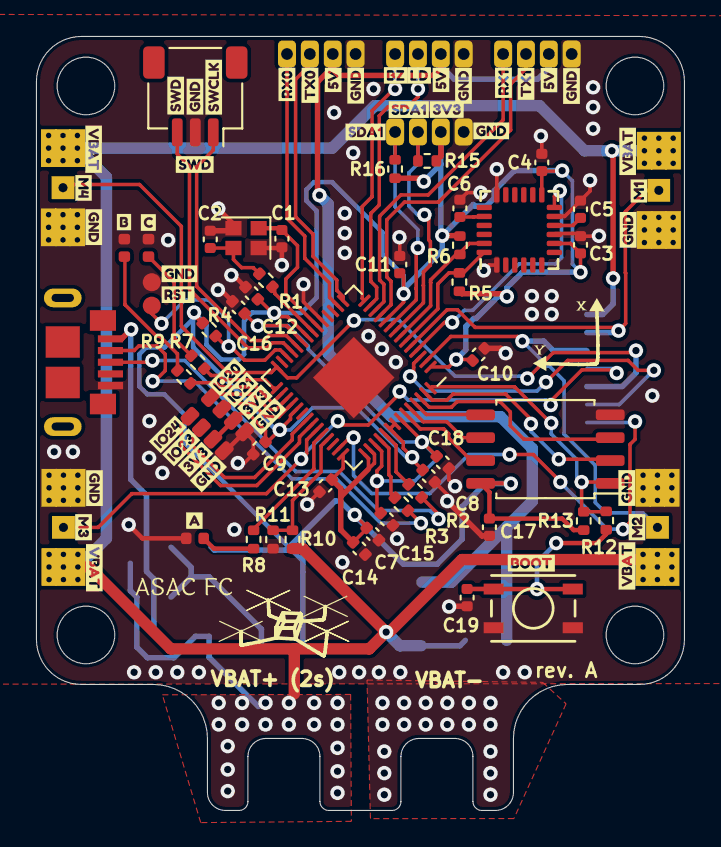
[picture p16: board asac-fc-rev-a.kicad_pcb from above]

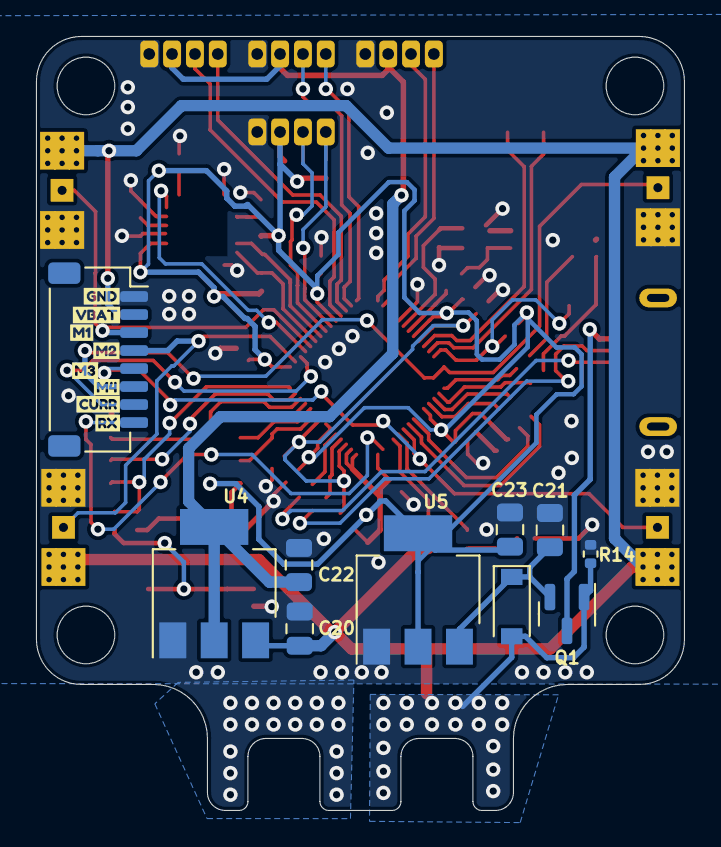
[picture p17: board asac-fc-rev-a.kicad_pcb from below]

Board: 2 copper layers, 36.0 x 43.0 mm, 119 parts (18 on the bottom side), 54 nets.

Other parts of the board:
kibuzzard-6408FA6D, kibuzzard-6408FA6D#2, kibuzzard-6408FA6D#3, kibuzzard-6408FA6D#4: G***; kibuzzard-6408FA6D
kibuzzard-6408FA39: G***; kibuzzard-6408FA39
kibuzzard-6408FA47: G***; kibuzzard-6408FA47
kibuzzard-6408FA74, kibuzzard-6408FA74#2, kibuzzard-6408FA74#3: G***; kibuzzard-6408FA74
kibuzzard-6408FAC1: G***; kibuzzard-6408FAC1
kibuzzard-6408FAC8: G***; kibuzzard-6408FAC8
kibuzzard-6408FB3B: G***; kibuzzard-6408FB3B
kibuzzard-6408FB51: G***; kibuzzard-6408FB51
kibuzzard-6408FBAE: G***; kibuzzard-6408FBAE
kibuzzard-6408FBBA: G***; kibuzzard-6408FBBA
kibuzzard-6408FC3B: G***; kibuzzard-6408FC3B
kibuzzard-6408FC28: G***; kibuzzard-6408FC28
kibuzzard-6408FC36: G***; kibuzzard-6408FC36
kibuzzard-6408FC56: G***; kibuzzard-6408FC56
kibuzzard-6408FD3E, kibuzzard-6408FD3E#2, kibuzzard-6408FD3E#3, kibuzzard-6408FD3E#4: G***; kibuzzard-6408FD3E
kibuzzard-6408FD16: G***; kibuzzard-6408FD16
kibuzzard-6408FD22, kibuzzard-6408FD22#2, kibuzzard-6408FD22#3, kibuzzard-6408FD22#4: G***; kibuzzard-6408FD22
kibuzzard-6408FDA0: G***; kibuzzard-6408FDA0
kibuzzard-6408FDC2: G***; kibuzzard-6408FDC2
kibuzzard-6408FDE1: G***; kibuzzard-6408FDE1
kibuzzard-64090C7A: G***; kibuzzard-64090C7A
kibuzzard-64090F7E: G***; kibuzzard-64090F7E
kibuzzard-64090F8A: G***; kibuzzard-64090F8A
kibuzzard-64090F8F: G***; kibuzzard-64090F8F
kibuzzard-64090F9C: G***; kibuzzard-64090F9C
kibuzzard-64090F56: G***; kibuzzard-64090F56
kibuzzard-64090F66: G***; kibuzzard-64090F66
kibuzzard-64090F74: G***; kibuzzard-64090F74
kibuzzard-64090F95: G***; kibuzzard-64090F95
kibuzzard-640900D1: G***; kibuzzard-640900D1
kibuzzard-640901D1: G***; kibuzzard-640901D1
kibuzzard-640901E3: G***; kibuzzard-640901E3
kibuzzard-640905D0: G***; kibuzzard-640905D0
kibuzzard-640910AE, kibuzzard-640910AE#2: G***; kibuzzard-640910AE
kibuzzard-640910C2: G***; kibuzzard-640910C2
kibuzzard-640911E9: G***; kibuzzard-640911E9
kibuzzard-640911EE: G***; kibuzzard-640911EE
kibuzzard-6409014C: G***; kibuzzard-6409014C
kibuzzard-6409115F: G***; kibuzzard-6409115F
kibuzzard-64090145: G***; kibuzzard-64090145
kibuzzard-64091195, kibuzzard-64091195#2: G***; kibuzzard-64091195

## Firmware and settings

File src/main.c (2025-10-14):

#include "hal.h"
#include "motor.h"
#include "ahrs.h"
#include "rc.h"
#include "imu.h"
#include "controller.h"
#include "led.h"
#include "battery.h"
#include "state.h"
#include "param.h"
#include "mavlink_driver.h"
#include "controller.h"

#include "scheduler.h"

static void init_driver(int (*init_function)(), const char* name);

static int driver = 0;
static int init_result = 0;


void test_print()
{
    //gcs_printf(MAV_SEVERITY_INFO, "BUS: %d, FREQ: %d, SDA: %d, SCL: %d", hal_i2c1.nbr, hal_i2c1.config.freq, hal_i2c1.config.sda, hal_i2c1.config.scl);
}

task_t tasks[] =
{
    {.update = imu_update,            .name = "IMU",     .loop_divider = 1},
    {.update = controller_pid_loop,   .name = "PID",     .loop_divider = 1},
    {.update = ahrs_update,           .name = "AHRS",    .loop_divider = 1},
    {.update = mavlink_driver_update, .name = "MAVLink", .loop_divider = 1},
    {.update = hal_serial_update,     .name = "Serial",  .loop_divider = 1},
    {.update = rc_update,             .name = "RC",      .loop_divider = 2},
    {.update = battery_update,        .name = "Battery", .loop_divider = 10},
    {.update = test_print,            .name = "TEST", .loop_divider = 1000}
};

int main()
{
    // Read params from EEPROM/FLASH - This must be done first, as much of the board-specific stuff is defined in params, instead of compile-time.
    params_init();

    // Initialize HAL - Serial, SPI, I2C etc. This also includes buffer initialization for the buses
    hal_init();
    
    // Initialize USB serial to allow messages to be sent/buffered to GCS
    mavlink_driver_init();

    // Initialize all drivers
    state.mode = MODE_BOOTING;
    gcs_printf(MAV_SEVERITY_INFO, "ASAC Booting up");

    // Initialize LED driver and blink boot-up sequence
    init_driver(led_init, "Led");
    led_run_boot_sequence();
    led1_on();

    // Initialize rest of drivers
    init_driver(battery_init,    "Battery");
    init_driver(imu_init,            "IMU");
    init_driver(controller_init,     "Controller");
    init_driver(motors_init,         "Motors");
    init_driver(rc_init,             "Receiver");
    init_driver(ahrs_init,             "AHRS");

    // At last we'll initialize the controller
    init_driver(controller_init,         "Controller");

    // Initialize scheduler
    scheduler_init(tasks, sizeof(tasks) / sizeof(task_t));

    // Done booting
    led1_off();
    led2_on();
    state.mode = MODE_IDLE;
    gcs_printf(MAV_SEVERITY_INFO, "Drivers initialized, let's go!");

    // Start scheduler, this will never return, let's go!
    scheduler_run();

    return 0;
}


// -- Helper functions -- //
static void init_driver(int (*init_function)(), const char* name)
{
    int res = init_function();

    if (res == 0) {
        gcs_printf(MAV_SEVERITY_DEBUG, "Init [OK] %s", name);
    } else {
        gcs_printf(MAV_SEVERITY_ERROR, "Init [ER] %s: (%d)", name, res);
    }

    driver++;

    // Update initresult bitmask
    init_result |= (res << driver);
}

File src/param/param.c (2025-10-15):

#include "param.h"

#include "hal.h"
#include "rc/rc.h"
#include "serial.h"
#include "mavlink_driver/mavlink_driver.h"
#include "state.h"
#include "ahrs.h"
#include "motor.h"

// -- Motor -- //
float mot_pwm_min;
float mot_pwm_max;
float mot_spin_arm;
float mot_spin_max;
float mot_pwm_type;

// -- Flight modes and channels -- //
float fltmode1;
float fltmode2;
float fltmode3;
float fltmode_channel;
float roll_channel;
float pitch_channel;
float yaw_channel;
float throttle_channel;
float arm_channel;
float arm_pwm_min;
float arm_pwm_max;

// -- RC -- //
float rc_protocol;
float rc_timeout;
float rc_max;
float rc_mid;
float rc_min;
float rc_dz;

// -- Tuning -- //
float atc_rat_rll_p;
float atc_rat_rll_i;
float atc_rat_rll_d;
float atc_rat_rll_ff;
float atc_rat_rll_imax;
float atc_rat_pit_p;
float atc_rat_pit_i;
float atc_rat_pit_d;
float atc_rat_pit_ff;
float atc_rat_pit_imax;
float atc_rat_yaw_p;
float atc_rat_yaw_i;
float atc_rat_yaw_d;
float atc_rat_yaw_ff;
float atc_rat_yaw_imax;

// -- Rate -- //
float max_roll_rate;
float max_pitch_rate;
float max_yaw_rate;

// -- IMU -- //
float imu_calib_gyro_on_boot;
float imu_offset_x;
float imu_offset_y;
float imu_offset_z;
float imu_accelcal_x;
float imu_accelcal_x;
float imu_accelcal_x;

// -- Hardware - Board specific -- //

// Battery pins
float brd_bat_volt;
float brd_bat_curr;
float brd_bat_volt_scaler;
float brd_bat_curr_scaler;

// Motor
float brd_mot1;
float brd_mot2;
float brd_mot3;
float brd_mot4;

// I2C 2
float brd_i2c1_sda;
float brd_i2c1_scl;
float brd_i2c1_freq;

// I2C 1
float brd_i2c2_sda;
float brd_i2c2_scl;
float brd_i2c2_freq;

// SPI 1
float brd_spi1_mosi;
float brd_spi1_miso;
float brd_spi1_clk;
float brd_spi1_freq;

// SPI 2
float brd_spi2_mosi;
float brd_spi2_miso;
float brd_spi2_clk;
float brd_spi2_freq;

// Serial 1
float brd_serial1_rx;
float brd_serial1_tx;
float brd_serial1_baud;
float brd_serial1_protocol;

// Serial 2
float brd_serial2_rx;
float brd_serial2_tx;
float brd_serial2_baud;
float brd_serial2_protocol;

// LEDs
float brd_led1;
float brd_led2;
float brd_led3;

// IMU
float brd_imu_type;
float brd_imu_bus;
float brd_imu_ss;

// AHRS
float ahrs_orientation;

// Scheduler
float sched_loop_rate;


mav_param_t mav_params[] = {
    // Motor
    {"MOT_PWM_MIN",  &mot_pwm_min},
    {"MOT_PWM_MAX",  &mot_pwm_max},
    {"MOT_SPIN_ARM", &mot_spin_arm},
    {"MOT_SPIN_MAX", &mot_spin_max},
    {"MOT_PWM_TYPE", &mot_pwm_type},

    // Flight modes and channels
    {"FLTMODE_CH", &fltmode_channel},
    {"FLTMODE1",   &fltmode1},
    {"FLTMODE2",   &fltmode2},
    {"FLTMODE3",   &fltmode3},
    {"ARM_CH",     &arm_channel},
    {"ARM_PWM_MIN",    &arm_pwm_min},
    {"ARM_PWM_MAX",    &arm_pwm_max},
    {"RLL_CH",     &roll_channel},
    {"PIT_CH",    &pitch_channel},
    {"YAW_CH",    &yaw_channel},
    {"THR_CH",    &throttle_channel},

    // RC
    {"RC_PROTOCOL", &rc_protocol},
    {"RC_TIMEOUT", &rc_timeout},
    {"RC_MAX", &rc_max},
    {"RC_MID", &rc_mid},
    {"RC_MIN", &rc_min},
    {"RC_DZ", &rc_dz},

    // Tuning
    {"ATC_RAT_RLL_P",    &atc_rat_rll_p},
    {"ATC_RAT_RLL_I",    &atc_rat_rll_i},
    {"ATC_RAT_RLL_D",    &atc_rat_rll_d},
    {"ATC_RAT_RLL_FF",    &atc_rat_rll_ff},
    {"ATC_RAT_RLL_IMAX", &atc_rat_rll_imax},

    {"ATC_RAT_PIT_P",    &atc_rat_pit_p},
    {"ATC_RAT_PIT_I",    &atc_rat_pit_i},
    {"ATC_RAT_PIT_D",    &atc_rat_pit_d},
    {"ATC_RAT_PIT_FF",    &atc_rat_pit_ff},
    {"ATC_RAT_PIT_IMAX", &atc_rat_pit_imax},

    {"ATC_RAT_YAW_P",    &atc_rat_yaw_p},
    {"ATC_RAT_YAW_I",    &atc_rat_yaw_i},
    {"ATC_RAT_YAW_D",    &atc_rat_yaw_d},
    {"ATC_RAT_YAW_FF",    &atc_rat_yaw_ff},
    {"ATC_RAT_YAW_IMAX", &atc_rat_yaw_imax},

    // IMU
    {"INS_GYR_CAL",   &imu_calib_gyro_on_boot},
    {"INS_GYROFFS_X", &imu_offset_x},
    {"INS_GYROFFS_Y", &imu_offset_y},
    {"INS_GYROFFS_Z", &imu_offset_z},
    {"INS_ACCSCAL_X", &imu_accelcal_x},
    {"INS_ACCSCAL_Y", &imu_accelcal_x},
    {"INS_ACCSCAL_Z", &imu_accelcal_x},

    // Rate
    {"ATC_RAT_RLL_MAX", &max_roll_rate},
    {"ATC_RAT_PIT_MAX", &max_pitch_rate},
    {"ATC_RAT_YAW_MAX", &max_yaw_rate},

    // Hardware - Board specific
    {"BRD_BAT_VOLT",  &brd_bat_volt},
    {"BRD_BAT_CURR",  &brd_bat_curr},
    {"BRD_VOLT_SCAL", &brd_bat_volt_scaler},
    {"BRD_CURR_SCAL", &brd_bat_curr_scaler},

    {"BRD_I2C1_SDA",  &brd_i2c1_sda},
    {"BRD_I2C1_SCL",  &brd_i2c1_scl},
    {"BRD_I2C1_FREQ", &brd_i2c1_freq},

    {"BRD_I2C2_SDA",  &brd_i2c2_sda},
    {"BRD_I2C2_SCL",  &brd_i2c2_scl},
    {"BRD_I2C2_FREQ", &brd_i2c2_freq},

    {"BRD_SPI1_MOSI", &brd_spi1_mosi},
    {"BRD_SPI1_MISO", &brd_spi1_miso},
    {"BRD_SPI1_CLK",  &brd_spi1_clk},
    {"BRD_SPI1_FREQ", &brd_spi1_freq},

    {"BRD_SPI2_MOSI", &brd_spi2_mosi},
    {"BRD_SPI2_MISO", &brd_spi2_miso},
    {"BRD_SPI2_CLK",  &brd_spi2_clk},
    {"BRD_SPI2_FREQ", &brd_spi2_freq},
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

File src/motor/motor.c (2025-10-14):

#include "motor.h"
#include "mavlink.h"
#include "mavlink_driver.h"
#include "oneshot.h"
#include "pwm.h"
#include "util.h"
#include "hal.h"

#define PWM_PULSE_WIDTH          ((float) 0.05)
#define ONESHOT_125_PULSE_WIDTH  ((float) 0.125)
// TODO: Clean up logic here and make this a setting!
// TODO: Make this ifdef instead perhaps?
static float pulse_width = ONESHOT_125_PULSE_WIDTH;


extern float mot_pwm_max;
extern float mot_pwm_min;
extern float mot_spin_arm;
extern float mot_spin_max;
extern float mot_pwm_type;

extern float brd_mot1;
extern float brd_mot2;
extern float brd_mot3;
extern float brd_mot4;

#define MOTOR_PWM_LEVEL_SCALER ((uint16_t) 10000)

static bool initialzed_ok = false;
static int8_t motor_ids[4];

motor_output_t motors;


// -- Public API -- //

int motors_init() {

    uint16_t wrap;
    float clk_div;

    int res = 0;
    
    switch ((esc_protocol_t) mot_pwm_type) {
        case ESC_PROTOCOL_PWM:
            res |= hal_pwm_init(brd_mot1, &motor_ids[0]);
            res |= hal_pwm_init(brd_mot2, &motor_ids[1]);
            res |= hal_pwm_init(brd_mot3, &motor_ids[2]);
            res |= hal_pwm_init(brd_mot4, &motor_ids[3]);
            break;
        case ESC_PROTOCOL_ONESHOT_125:
        case ESC_PROTOCOL_ONESHOT_42:
        case ESC_PROTOCOL_MULTISHOT:
        default:
            gcs_printf(MAV_SEVERITY_WARNING, "Invalid ESC protocol: %d", mot_pwm_type);
            return -1;
    }

    if (res != 0) return res;

    res |= hal_pwm_set(motor_ids[0], 1000);
    res |= hal_pwm_set(motor_ids[1], 1000);
    res |= hal_pwm_set(motor_ids[2], 1000);
    res |= hal_pwm_set(motor_ids[3], 1000);

    if (res == 0)
    {
        initialzed_ok = true;
    }

    return res;
}

void set_motor_pwm(const uint8_t motor, const float pwm) {
    if (!initialzed_ok) return;

    float pulse;
    uint16_t pwm_value;

    switch ((esc_protocol_t) mot_pwm_type) {
        case ESC_PROTOCOL_PWM:
            // pwm: Value between 0-1.
            //printf("M: %d, Org: %f, pulse: %f, pwm_value: %d\n", motor, pwm, pulse, pwm_value);
            hal_pwm_set(motor_ids[motor], pwm);
            break;
        case ESC_PROTOCOL_ONESHOT_125:
        case ESC_PROTOCOL_ONESHOT_42:
            // Motor values are 1,2,3,4 ut oneshot expects 0,1,2,3
            //oneshot_set(motor-1, pwm);
            break;
        case ESC_PROTOCOL_MULTISHOT:
            break;
        default:
            break;
    }

}

void set_all_motors_pwm(const motor_output_t* motor_command) {
    set_motor_pwm(MOTOR_1, motor_command->m1);
    set_motor_pwm(MOTOR_2, motor_command->m2);
    set_motor_pwm(MOTOR_3, motor_command->m3);
    set_motor_pwm(MOTOR_4, motor_command->m4);

    if ((mot_pwm_type == ESC_PROTOCOL_ONESHOT_125) ||
        (mot_pwm_type == ESC_PROTOCOL_ONESHOT_42))
        {
            // Oneshot doesn't apply the values directly but writes them to
            // buffer, so we need to apply the values here.
            // This way, they are all synced.
            //oneshot_apply();
        }
}

// -- Private -- //
void motor_mixer_update(motor_output_t* output, const float roll, const float pitch, const float yaw, const float throttle)
{
    // This is mainly used for debugging and knowing if the mixer is saturated or not
    // motors.total = roll + pitch + yaw + throttle;
    // motors.c_total = constrain(motors.total, -1, 1);
    
    // Assuming Betaflights motor standard X:
    //  4 2
    //  3 1

    // Using Ardupilot default body frame, NED
    //  Roll positive  - Right
    //  Pitch positive - Upwards
    //  Yaw positive   - Right

    // Calculate throttle for each motor
    motors.m1 = -roll + pitch + yaw + throttle;
    motors.m2 = -roll - pitch - yaw + throttle;
    motors.m3 =  roll + pitch - yaw + throttle;
    motors.m4 =  roll - pitch + yaw + throttle;

    // Check if any motor is below 0. This would indicate that it should spin less than 0 which we can't.
    // In this case, we shift all motor outputs with this amount, to ensure we're in limits
    float min_motor = minf(minf(motors.m1, motors.m2), minf(motors.m3, motors.m4));
    if (min_motor < 0)
    {
        // Eg:        M1   M2   M3   M4
        //            0.6  0.2  0.5  -0.3
        // -> (+0.3)  0.9  0.5  0.8  0
        float shift = -min_motor;
        motors.m1 += shift;
        motors.m2 += shift;
        motors.m3 += shift;
        motors.m4 += shift;
    }

    // Check if any motor output is above 1, which means we're saturated too.
    // If this happens we scale all motor outputs evenly, so they are within 0-1.
    float max_motor = maxf(maxf(motors.m1, motors.m2), maxf(motors.m3, motors.m4));
    if (max_motor > 1)
    {
        // Eg:         M1   M2   M3   M4
        //             1.4  0.9  1.2  0.8
        // -> (*0.71)  1    0.6  0.9  0.6
        float scale = 1.0f / max_motor;
        motors.m1 *= scale;
        motors.m2 *= scale;
        motors.m3 *= scale;
        motors.m4 *= scale;
    }

    float pwm_min = mot_pwm_min + ((mot_pwm_max - mot_pwm_min) * mot_spin_arm);
    float pwm_max = mot_pwm_min + ((mot_pwm_max - mot_pwm_min) * mot_spin_max);
 
    // Map to pwm values
    output->m1 = (uint16_t) mapf(motors.m1, 0, 1, pwm_min, pwm_max);
    output->m2 = (uint16_t) mapf(motors.m2, 0, 1, pwm_min, pwm_max);
    output->m3 = (uint16_t) mapf(motors.m3, 0, 1, pwm_min, pwm_max);
    output->m4 = (uint16_t) mapf(motors.m4, 0, 1, pwm_min, pwm_max);
}


/*
    M4   M2
        \ /
        / \
    M3   M1

    M1 1, -1,  1, -1  <- Rear right
    M2 1, -1, -1,  1  <- Front right
    M3 1,  1,  1,  1  <- Rear left
    M4 1,  1, -1, -1  <- Front left
*/

// if (throttle < THROTTLE_MIN) {
//     throttle = THROTTLE_MIN;
// }
// motor_command->m1 = throttle - adjust->roll + adjust->pitch - adjust->yaw;
// motor_command->m2 = throttle - adjust->roll - adjust->pitch + adjust->yaw;
// motor_command->m3 = throttle + adjust->roll + adjust->pitch + adjust->yaw;
// motor_command->m4 = throttle + adjust->roll - adjust->pitch - adjust->yaw;

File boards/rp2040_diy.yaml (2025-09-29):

hal: rp2040

defaults:
  BRD_IMU_TYPE: 1 # MPU6050
  INS_IMU_BUS:  1 # I2C1
  BRD_I2C2_SDA: 4 # GP4
  BRD_I2C1_SCL: 5 # GP5
  BRD_I2C1_FREQ: 400000 # 400 kHz
  BRD_LED1: 19 # GP19
  BRD_LED2: 20 # GP20

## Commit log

2023-03-15 Created frame for 3d printing
    [Body-Lower.stl, Body-Top.stl, LeftArm-rev-a.stl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]
2023-03-27 Swapped to using devboard rp pico and breakout board for MPU-6050 instead of custom pcb..
    [controller.c, imu.c, led.c]
2023-03-27 Added some 3d models
    [asac-fc-frame-rev-a.FCStd]
2023-03-27 Added kicad pcb
    [asac-fc-rev-a.csv]
2023-03-28 Created driver for mpu6050. Seems like a reading takes ~450-500 us, which means we 1khz pid loop should be ok :)
2023-03-29 Added: - Battery adc module - vsrtos, and tested basic functionality. Need to test more - state handling - settings (write/read to flash)
2023-03-30 - Added logic to motor mixer - Added init method for pid-controller - Added more logic to controller_update() (PID-loop main function)
2023-04-01 - Some general cleanup - Change motor API, - Added arm state - Added connected state - First (unstable) takeoff done!
    [controller.c, led.c, main.c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]
2023-04-05 - Made controller variables public - Made PID variables public - Added debug pwm pin to motors - Changed type pid params to floats - Added timeout on i2c reading for mpu driver
2023-05-27 - Added packed attribute to log structs - Configured telemetry module and made it work. This was implemented with pio UART, seems to work pretty well, even with 921600 baudrate. - Added while loop to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
    [controller.c, main.c]
2023-05-28 - Added timer functions to asac_fc and fixed bug in them - Added data integrity protection to ibus module, by inspecting and validating the checksum. Also improved the state machine of the module. - 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
    [controller.c, imu.c, main.c]
2023-05-28 - Made monitor.py tool that automatically connects to serial port and prints incoming data - Made bash script that builds firmware and flashes through serial + reset, using picotool - Created quick a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
2023-05-31 First controlled take-off and flight, wehooo!! - Found CRUICAL reason why drone spun onctrollably around yaw axis, the Z from IMU was expected to be pointing DOWN according the the PID controller, bu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
    [controller.c, imu.c, main.c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]
2023-06-04 - Removed reading acc data from imu to save reading time. - Cleaned up control update function. - Tuned PID params after flying, increased quite a bit - Made TELEMETRY_LOGGING define to enable/disabl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
2023-06-07 Created new revision for PCB: - Switched to USB-C - Switched IMU to BMI270 - Removed connectors on bottom side for ESC - Switched to 4 layer board
    Ordered it, this time with PCB assembly on top side,
    since I had big issues with soldering the IMU by hand
    last time. Let's hope this rev goes better!
    [BOM-asac-fc-rev-b.csv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]
2023-06-11 Added oneshot PIO implementation. This utilizes the entire PIO1 block to send oneshot pulses to the motors. A great benefit of this is that the main processor doesn't have to do anything except for t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
    [controller.c, motor.c, oneshot.c]
2023-06-14 Some general cleanup - Created separate folder in cad directory - Added README.md for each directory - Added some description for makefile targets
    [Body-Lower.stl, Body-Top.stl, LeftArm-rev-a.stl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]
2023-06-20 Started on migration to support PCB rev. B - Added BMI270 Sensor API submodule, and wrote a wrapper around it to make it use rp2040s SPI drivers. Seems to work OK! - Changed PIN definitions in "machi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
2023-06-28 IMU improvements
    - Added configuration initialization of IMU BMI270,
    both for gyro and accel.
    - Made custom imu_read function, since the one in
    BOSCHs driver was a bit slow. Reduced total IMU
    reading time from ~450us to ~200us.
    - Added red led
    - Swapped M1 and M2 pins, since they were
    reversed on the PCB for rev 2.
    - Removed debug motor
    [bmi270_asac.c, imu.c, main.c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]
2023-06-28 Changed debug print every sec check to #ifdef for vsrtos
2023-06-29 pico-sdk submodule - Added pico-sdk as a submodule, and changed the path in CMakeLists.txt to using relative path for the sdk instead of absolute like before. - Added comment in Makefile regarding ab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
2023-07-02 MAVlink params and settings
    - Added MAVlink parameters that will serve as system
    settings and be saved on flash.
    - Made settings work by storing the parameters to flash.
    - Added handlers in serial_mavlink to handle incoming
    MAVlink requests.
    - Extended state_t to include attitude, velocity, position etc
    - Added state estimation in controller. The estimation for attitude
    is not tested yet, so probably doesn't work.
    [controller.c, main.c]
2023-07-18 Added some info about new pcb and updated README git some images. Also exported schematic as PDF.
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2023-08-27 Added initial CRSF and refactored receiver code
    - Added initial support for CRSF. This commit only includes reading
    CRFS frames, and so far only channel data and link statistics frames
    are parsed.
    - Moved ibus & crsf into separate rc directory, with a "generic"
    rc file "rc.h". The idea here is that each RC protocol should be
    able to fill an `rx_state_t` with correct information.
    - Made `receiver.h` more generic and it now looks at the system
    settings to decide which RX protocol to use.
    CRSF seems to work OK, but haven't done any
    flying with it yet
    [controller.c, main.c]
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2023-08-27 Serial mavlink refactorization
    - Cleaned up a bit in the serial mavlink handler.
    - Added check for USB voltage before trying to send/read any data
    through the serial port. This is added because if we're not connected
    to USB, there's no point to try to read data, nor send anything.
    - Created 1 single task for all mavlink communication instead of
    separate ones. Inside this task the timing for periodic messages
    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
2023-09-06 Added param print to main and some cleanup
    Also made serial mavlink periodically send RC channel data every 100ms
2023-09-16 Fixed some compilation warnings
    [bmi270_asac.c]
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2023-09-16 Added mavlink test motor throttle
    This can be very useful if you want to test the motors from a GUI.
    I'm not 100% sure that I'm treating the MAV_CMD_DO_MOTOR_TEST
    command as expected, but atm it simply force-sets the throttle of the
    given motor. Once this has been called, asac will never arm normally
    until rebooted, since the force-arm flag has been set.
    [controller.c]
2023-09-16 Added support for mavlink statustext
    This can be very useful to debug print messages to GCS
2023-09-16 Added minor comment to clear up PCB mistake
2023-09-16 Fixed incorrect motor PWM pulse length
    [motor.c]
2023-09-16 Fixed bug with old reference to rx_protocol
    [main.c]
2023-09-16 Removed blue LED set from init.
    This is handled by the RC connect logic instead
2023-09-16 Renamed PID feedforward params
    MAVLINK params are max 16 chars, and
    with "ff" at the end they are 17..
    Changed to "_f" to be consistent between param_id
    and variable name.
2023-09-16 Fixed multicore write flash bug
    It seems like we need extra care when writing to flash on
    the second core.
    This commit adds some stuff that should but the primary core
    in a blocked state, before writing to flash.
    Hopefully this will work fine.
    [main.c]
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2023-09-16 Minor cleanup
    - Removed unnecessary function
    - Fixed bug when printing mavlink statustext, since the method
    expects a char buffer of size 50.
    - Added extra debug print info when writing to flash
2023-09-19 Throttle scaling fix
    Fixed "proper" scaling of throttle. Before, when throttling
    a little bit (1000-THROTTLE_MIN) nothing would happen.
    This is because the throttle value was not offset THROTTLE_MIN.
    [controller.c]
2023-09-19 Fixed vbat ADC
    The ADC seems to be lagging so might need to check the filtering
    and software settings for this.
    [controller.c]
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2023-09-19 Added pid_reset after `arm()`
    This is nice because now we always start with fresh PID values after
    arming. Before this was just done after disarm.
2025-09-26 Big refactor towards supporting different HALs
    Compiles OK
    [BOM-asac-fc-rev-b.csv, Body-Lower.stl, Body-Top.stl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]
2025-09-26 Refactor continuation!
    Removed vsrtos - Decided to use stick to ASAC and keep it all in a single loop int main()
    Can run different functions at different frequencies.
    Just as before, nothing is allowed to block, so everything gotta be quick and use DMA/IRQ to transfer data, no busywait...
    Can compile just fine for SITL which is great.
2025-09-27 Changed init printf to gcs_printf This way we can get it through mavlink
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2025-09-29 Param: Added some missing parameters for the updated hal
    [param.c]
2025-09-29 Scheduler: Initial implementation.
    Implements a frame-based cooperative scheduler:
    - Runs at fixed loop rate (50–2000 Hz)
    - Tasks registered with loop dividers (run every N frames)
    - Tracks exec time (min/max/avg), missed frames, and counts
    - Currently "idle task" is just hal_sleep but can be replaced
    - Adds CPU load calculation (instant + EMA avg)
    [param.c, scheduler.c]
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2025-09-30 Tests: Tried Unity testing framework
    Seems to work OK, let's see how it is to use.
    When building for SITL we also build tests.
    Run with `make test`
2025-09-30 HAL: Serial update all buses instead of single
    Same thing goes for i2c and spi!
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2025-10-03 Controller(s): Cleanup, rename and refactor
    Clearer separation. `controller` is the main controller that uses atrc (Attitude Rate Controller) and throttle controller to get pid outputs that is fed to the motor mixer.
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2025-10-03 Battery: Fixed double header defguard
2025-10-03 Battery: Added frontend init method
    Clearer separation between frontend and backend.
    This way we can have different battery backends, similar to how AP has different battery monitor types
2025-10-03 Pid: Cleanup and refactor
    I feel like this implementation is more clean and simpler.
    We skip everything with timing-related I-term antiwindup and simply
    let the pid control take a bool if it should ignore I term or not
    This way it's easy for the callers to tell it to prevent I-term buildup (we still hav `imax` the limits the value of I-term.
    Also, the pid should now not be tied to the flight control (which it was before, due to throttle argument)
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2025-10-03 Bug: Prevent pid dt divide by 0
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2025-10-04 I2C: Added bus probing
    This can be super useful for debugging what devices are connected
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2025-10-04 Refactor: Changed pid_t to pid_handle_t
    pid_t seems used by the arm compiler (for process id), so we'll rename it
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2025-10-04 Flash: Change default flash size to 2MB
    NOTE: This should not be in hal_flash.c but in board-specific build!!
2025-10-04 Hal: Changed name of reboot
    [hal.h]
2025-10-04 Mavlink: Added ability to reboot over mavlink
    Currently not supported by the sitl hal...
2025-10-04 Hal: Bug: Always initialize USB (serial 0)
    [hal.c]
2025-10-04 Hal: Bug: Prevent i2c/spi init with bad params
    [hal.c]
2025-10-04 Scheduler: Bug: Prevent scheduler ever sleeping for more than period time
    If there would be some kind of overflow/bug this clamping should be nice
    [scheduler.c]
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2025-10-04 Hal: busy-wait sleep instead of sleep_xx
    the sleep_xx seems to screw the debugger for some reason...
    It gets stuck when using sleep_ms()
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2025-10-04 Hal: Bug: initialized same i2c bus twice...
    [hal.c]
2025-10-04 Hal: Bug: i2c bus probing took wrong i2c bus
    [hal.c]
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2025-10-05 Hal: Fixed i2c bugs - Read and write didnt work with device addr and reg addr
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2025-10-05 Controller: Removed rc reading / filter from control loop
    This will be handle by rc_update() instead
2025-10-05 Sensor: Added sensor struct for health/enabled etc Useful for mavlink system status packet
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2025-10-14 Params: Added missing parameters
    [param.c]
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2025-10-14 Build: Fixed old renaming of sensors -> sensor
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2025-10-15 Bug: Fixed incorrect pwm microseconds
    Should probably change this in future so PWM isn't bound to be used for 1000-2000 pulses...
2025-10-15 HAL: ADC cleanup
    TODO: Support reading more than 1 channel on the rp2040 backend...

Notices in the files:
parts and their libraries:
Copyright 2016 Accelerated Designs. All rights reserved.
